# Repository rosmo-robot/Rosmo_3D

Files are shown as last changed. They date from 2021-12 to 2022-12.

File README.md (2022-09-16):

# Rosmo_3D

:warning: In development. 

It is part of the [rosmo.io](https://rosmo.io) project. You can find complete BOM on the Rosmo website.

What is Rosmo?

It's a modular set of open-hardware components that can be assembled into robots of different complexity and price.

It's all based on ESP32 so should support MicroROS work.

There are a number of different needs for 'starter' robot kits.

Software that's interesting to us right now includes:

Linorobot2 C++/ Platformio / Ros2

https://github.com/platisd/smartcar_shield/ C++/ Platformio/ Nice API

Hadabot (Micropython ROS2, Docker)

https://maker.makecode.com/#editor

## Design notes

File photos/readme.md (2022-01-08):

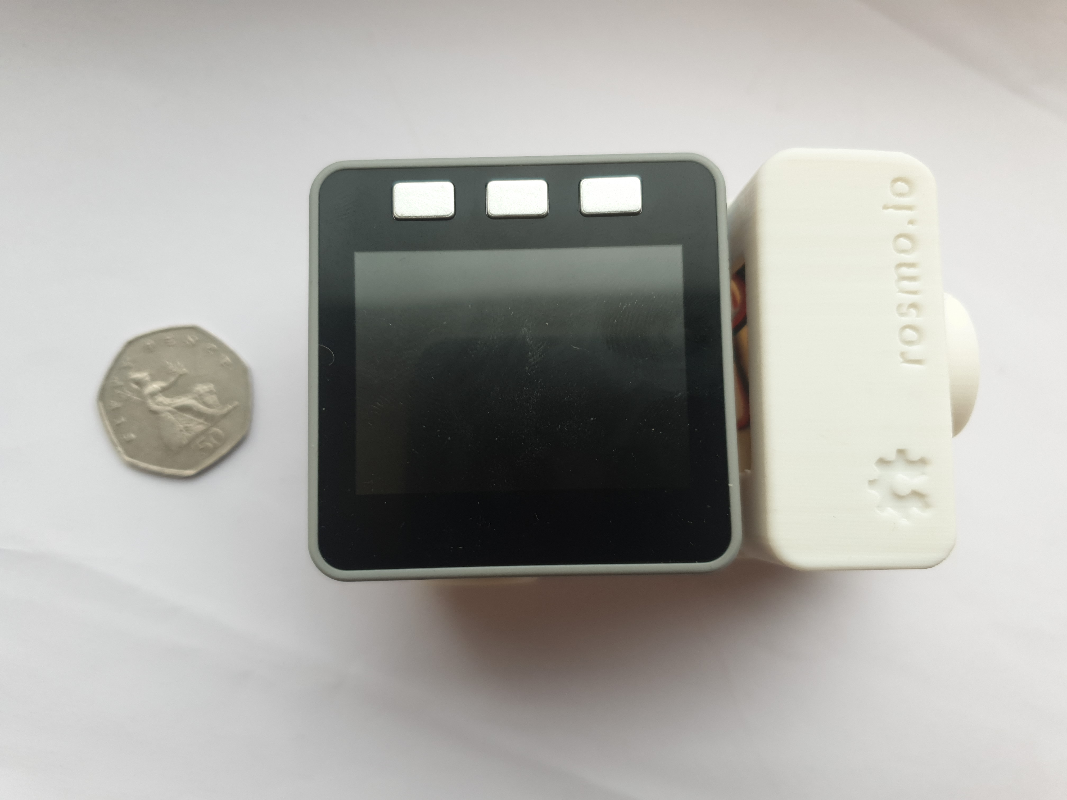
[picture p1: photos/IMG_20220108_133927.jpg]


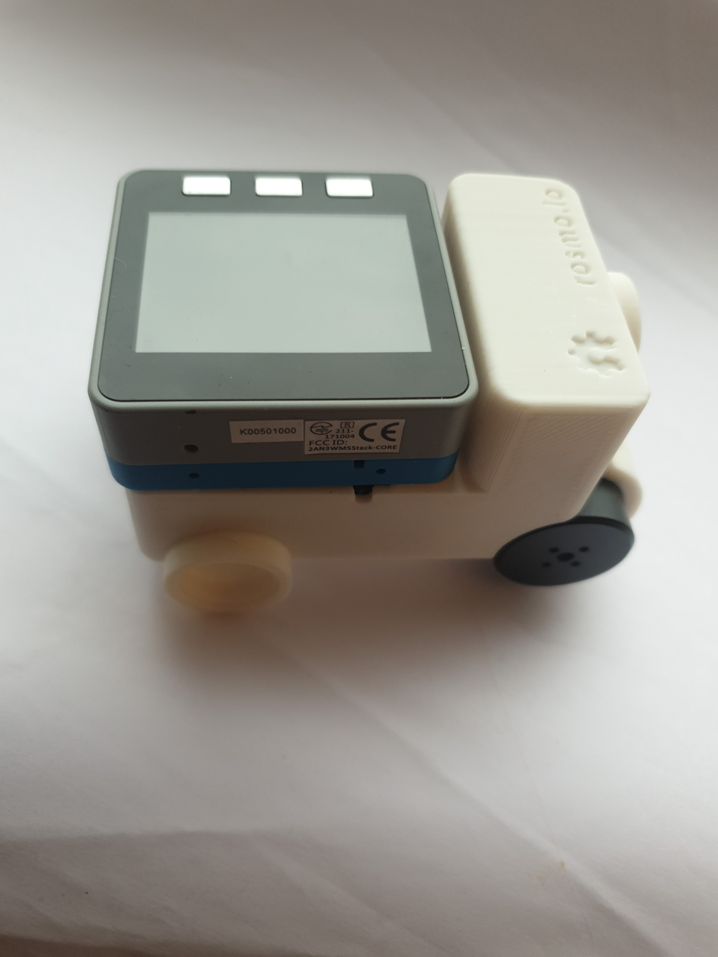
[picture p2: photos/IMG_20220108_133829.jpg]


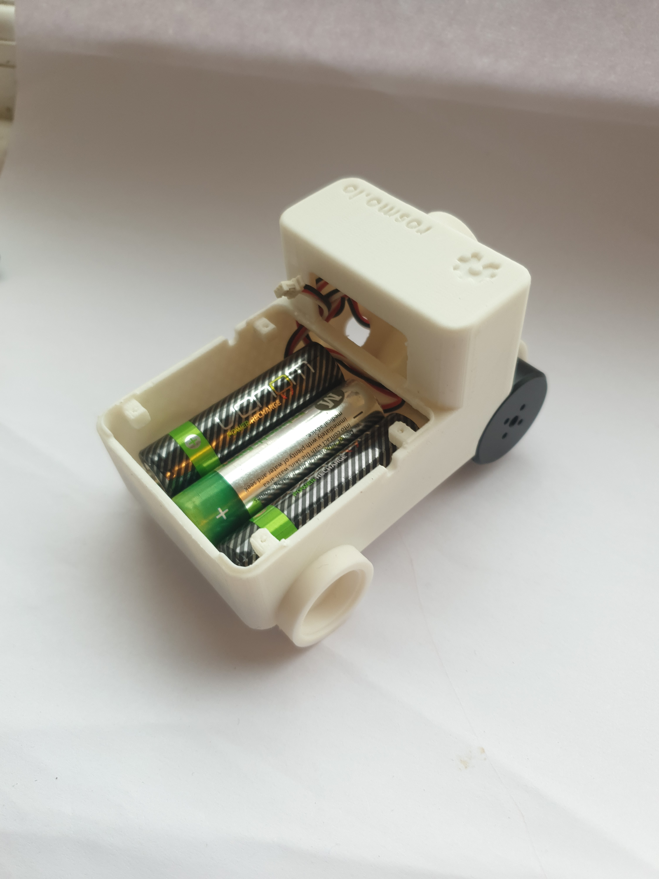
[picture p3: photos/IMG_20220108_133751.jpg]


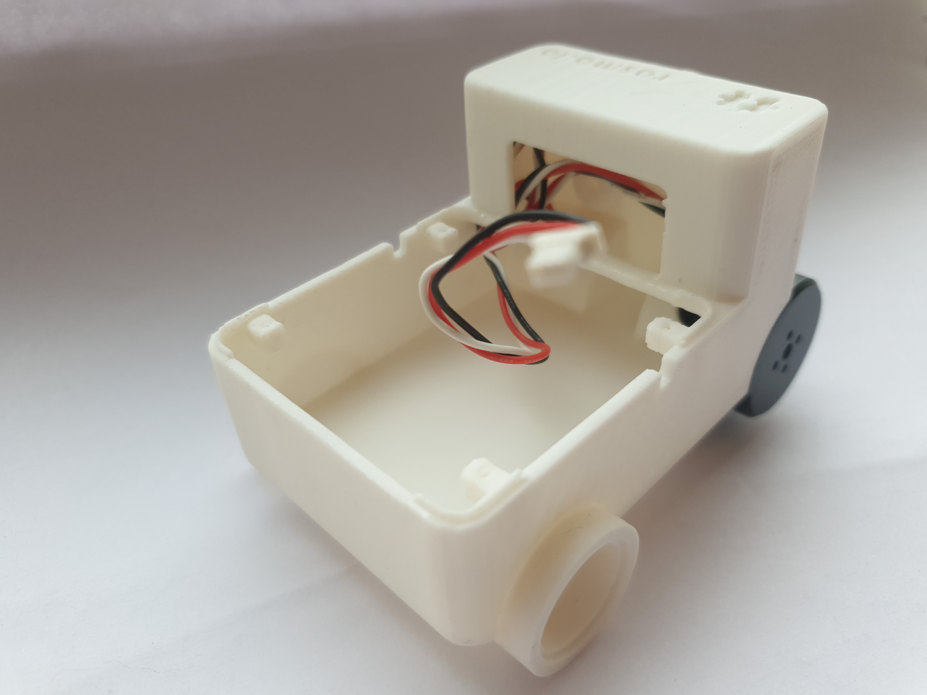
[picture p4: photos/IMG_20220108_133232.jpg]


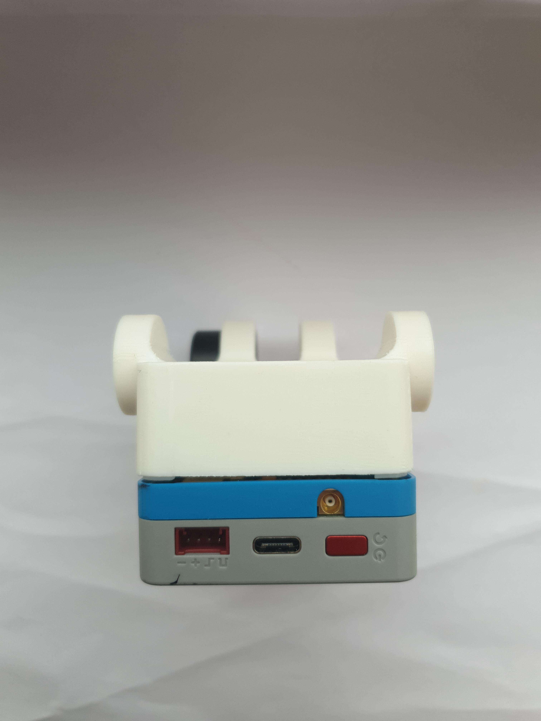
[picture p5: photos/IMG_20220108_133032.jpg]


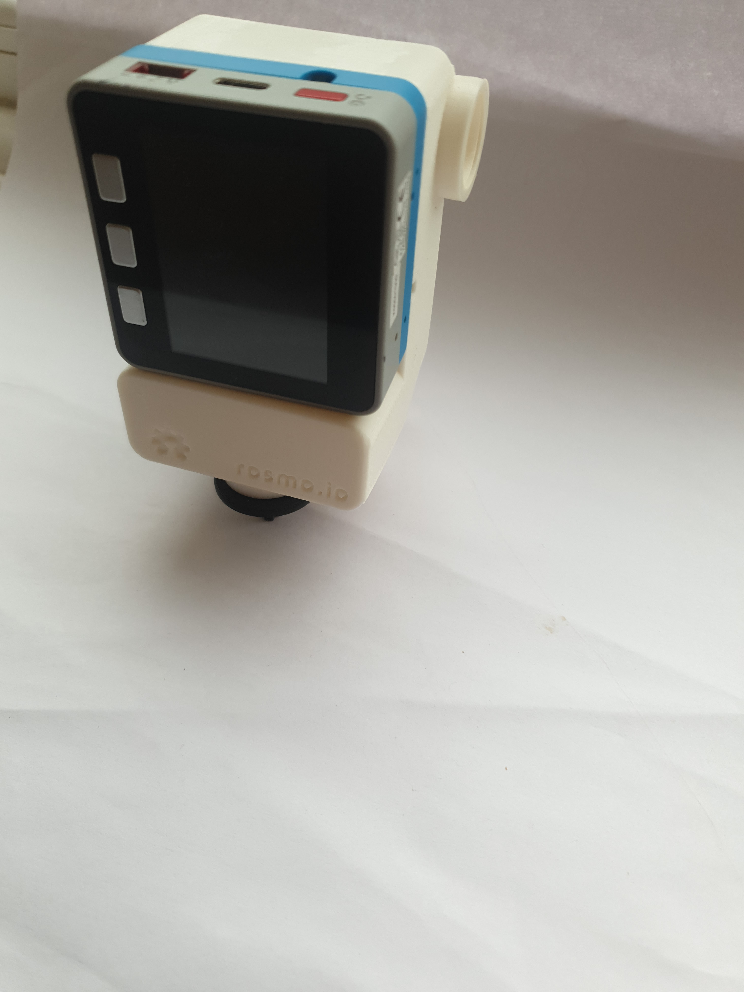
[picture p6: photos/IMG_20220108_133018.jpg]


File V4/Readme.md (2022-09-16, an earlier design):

## Brushed motor/encoder version

https://github.com/rosmo-robot/micro-bot/tree/master/Hardware/V2.11

### BLDC/encoder version additional parts

https://github.com/rosmo-robot/Rosmo_3D/blob/main/V4/BLDC/Readme.md

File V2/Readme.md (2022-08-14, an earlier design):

Design work is underway in this thread:[FreeCAD forum](https://forum.freecad.org/viewtopic.php?p=594216&sid=2a7ae776db8a154a61fe9510c4f52c36#p594216)

Check folder above with highest version number

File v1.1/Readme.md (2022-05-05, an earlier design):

This is a functional platform for motor testing

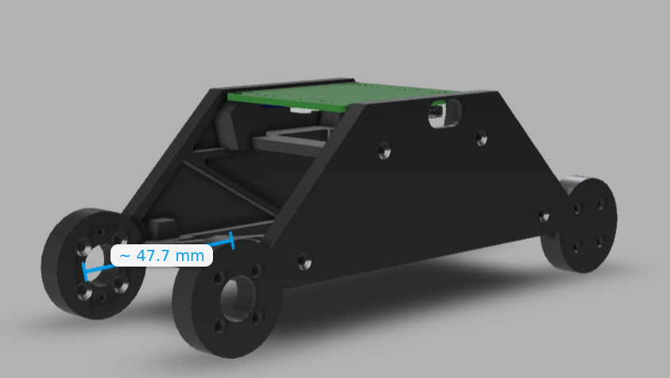
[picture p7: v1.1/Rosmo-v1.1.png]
This is an image


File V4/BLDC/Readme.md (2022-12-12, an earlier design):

### BLDC BOM

Battery

* 2x [pololu wheels](https://github.com/rosmo-robot/Rosmo_3D/blob/main/V4/pololu-rear-12mm_v4.FCStd) ([FCSTD](https://github.com/rosmo-robot/Rosmo_3D/blob/main/V4/pololu-rear-12mm_v4.FCStd))
* 1x [CamcnewPareddownH.stl](https://github.com/rosmo-robot/Rosmo_3D/blob/main/V4/servo/camcnewParedDownH-Body001Pocket036.stl)  [(FCSTD)](https://github.com/rosmo-robot/Rosmo_3D/blob/main/V4/camcnewParedDownH.FCStd) 
* 2x [encoder.stl](https://github.com/rosmo-robot/Rosmo_3D/blob/main/V2/2.09/2.09-encoder.stl) ([FCSTD](https://github.com/rosmo-robot/Rosmo_3D/blob/main/V2/2.10/Encoder-mount-v2.10.FCStd))
* 1x [RPI.stl](https://github.com/rosmo-robot/Rosmo_3D/blob/main/V4/servo/RPI.stl) mount plate ([FCSTD](https://github.com/rosmo-robot/Rosmo_3D/blob/main/V4/BLDC/RosmoBattPlate.FCStd))
* 1x [BLDC driver board](https://github.com/Twisted-Fields/rp2040-motor-controller) Get xt60 plug on the power, 4mm female banana on the motor cables.
* 1x [1300mah 4s battery](https://www.aliexpress.com/item/33003200541.html) 
* 2x [Magnet_Holder.stl](https://github.com/rosmo-robot/Rosmo_3D/blob/a09dbaf5618fc7efe2f3068fb2b35d144179f3ac/V2/2.10/Magnet_Holder.stl)
* 2x [GB 2208 motors](https://www.aliexpress.com/wholesale?catId=0&initiative_id=SB_20220818074047&SearchText=gb2208)
* 1x [Huzzah 32 feather](https://www.adafruit.com/product/3405)
* 1x [Feather:bit](https://github.com/rosmo-robot/Feather-Bit/)
* 1x [16340 powerbank](https://www.aliexpress.com/item/32951637621.html)
* 1x [16340 battery](https://www.aliexpress.com/item/1005004385519421.html)

Plus you will need the [Pololu 22T kit](https://shop.pimoroni.com/products/pololu-track-set-1?variant=933150982154), or alternately print [2x front wheels](https://www.thingiverse.com/thing:885742) & [track](https://www.thingiverse.com/thing:1936113)

Or if you don't want Pololu tracks, check out the [Tamiya track parts](https://github.com/rosmo-robot/Rosmo_3D/tree/main/V2/optional-tracks)

## Optional extras

 * [2.4" screen](https://www.aliexpress.com/item/1005003936535877.html)

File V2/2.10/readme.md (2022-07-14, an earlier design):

This model was made by [Bance on FreeCAD](https://forum.freecadweb.org/viewtopic.php?p=596344#p596344). It is released under a [CERN-OHL-P licence](https://github.com/rosmo-robot/Rosmo_3D/blob/main/LICENSE)

*untested 

You will need to print

* 1x v2.10-Body.stl
* 1x 2.10-battery-clip.stl
* 2x Magnet_Holder.stl
* 2x pololu-rear.stl
* 2x Encoder-mount-v2.stl

Plus you will need the [Pololu 22T kit](https://shop.pimoroni.com/products/pololu-track-set-1?variant=933150982154), or alternately print [2x front wheels](https://www.thingiverse.com/thing:885742) & [track](https://www.thingiverse.com/thing:1936113)

Or if you don't want Pololu tracks, check out the [Tamiya track parts](https://github.com/rosmo-robot/Rosmo_3D/tree/main/V2/optional-tracks)

# Changelog

1. Expanded encoder sockets
2. Motor cable can now go out up from encoder mount
3. Main tray trimmed/extended as required.
4. Changed bolt holes to through all.

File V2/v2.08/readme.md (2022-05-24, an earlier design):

The axel nut housings were too small, resized.

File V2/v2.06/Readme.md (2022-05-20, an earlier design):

This model was made by [Bance on FreeCAD](https://forum.freecadweb.org/viewtopic.php?p=596344#p596344). It is released under a [CERN-OHL-P licence](https://github.com/rosmo-robot/Rosmo_3D/blob/main/LICENSE)

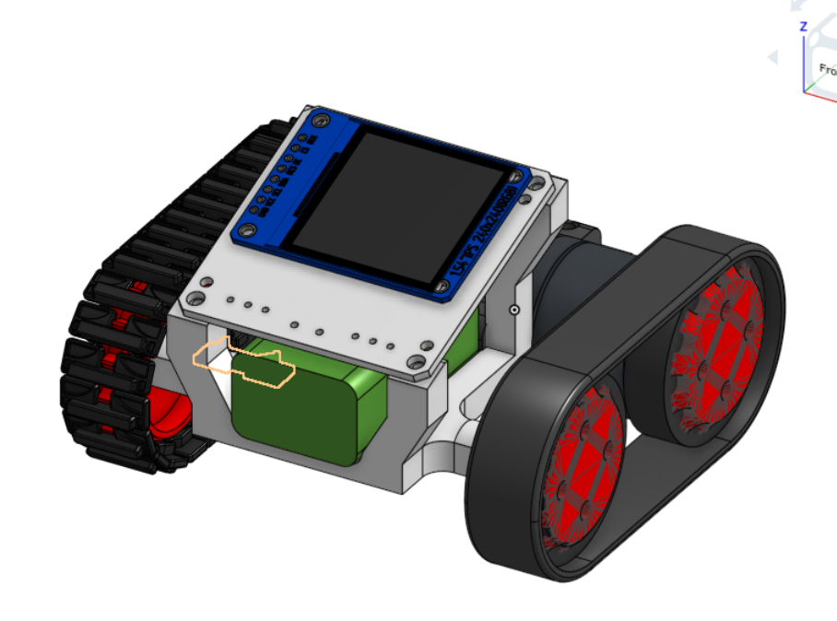
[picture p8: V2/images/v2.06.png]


[View model](https://cad.onshape.com/documents/1616bde745e05690bd2f50e3/w/f603a4efa7320437acad7441/e/d3c72be522508f10a3753235)

*untested 

You will need to print

* 1x v206.stl
* 2x Magnet_Holder.stl
* 2x pololu-rear-3.4mm.stl
* 2x v206-encoder.stl

Plus you will need the [Pololu 22T kit](https://shop.pimoroni.com/products/pololu-track-set-1?variant=933150982154), or alternately print [2x front wheels](https://www.thingiverse.com/thing:885742) & [track](https://www.thingiverse.com/thing:1936113)

Or if you don't want Pololu tracks, check out the [Tamiya track parts](https://github.com/rosmo-robot/Rosmo_3D/tree/main/V2/optional-tracks)

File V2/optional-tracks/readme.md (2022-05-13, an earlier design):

In addition to the Pololu tracks we would like to support Tamiya tracks

The Sprocket for these is https://github.com/rosmo-robot/Rosmo_3D/blob/main/V2/Sprocket.stl

It needs to be adapted as a front wheel with the [same  4mm  hole as the pololu](https://www.pololu.com/file/0J1359/pololu-track-set-dimensions.pdf)

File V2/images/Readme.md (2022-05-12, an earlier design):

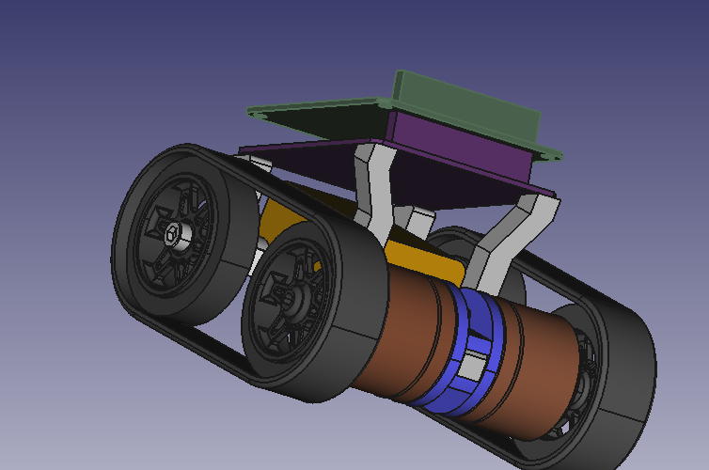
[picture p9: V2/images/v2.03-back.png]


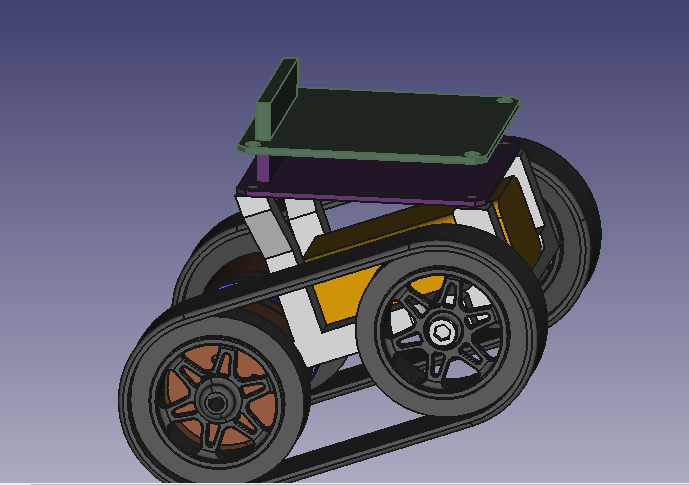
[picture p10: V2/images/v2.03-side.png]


T
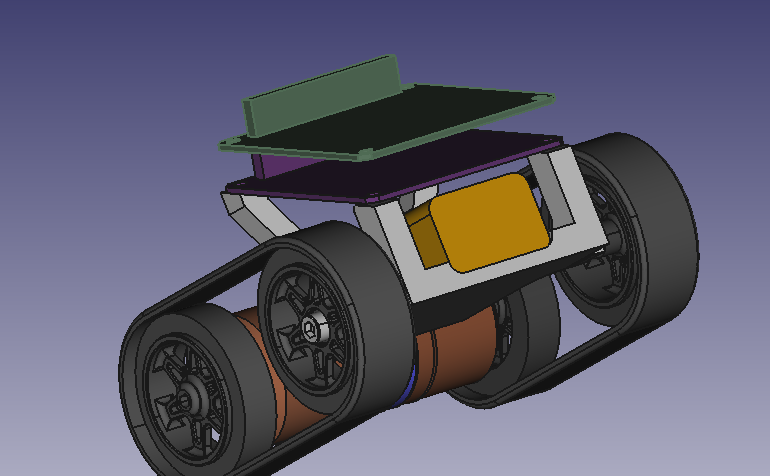
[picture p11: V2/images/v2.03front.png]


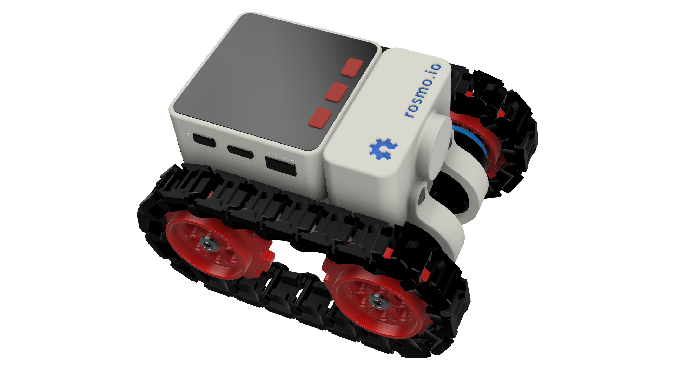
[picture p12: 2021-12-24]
rosmo.png

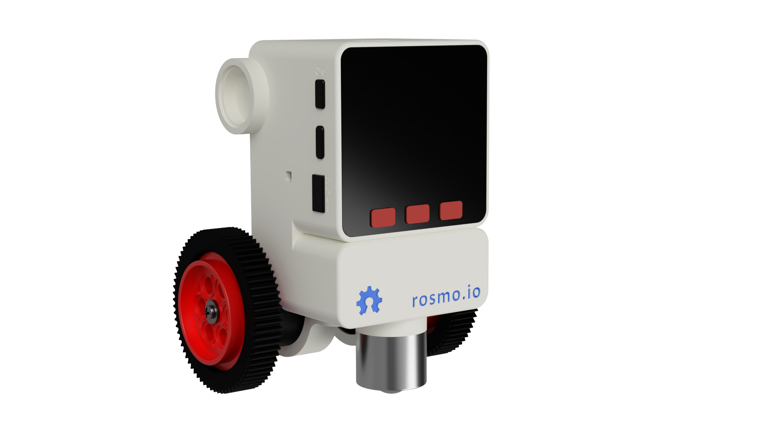
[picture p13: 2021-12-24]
wheel_mode.png

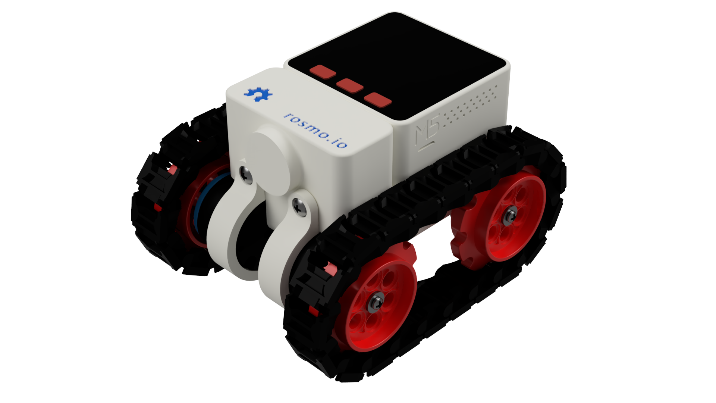
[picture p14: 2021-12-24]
track_mode.png

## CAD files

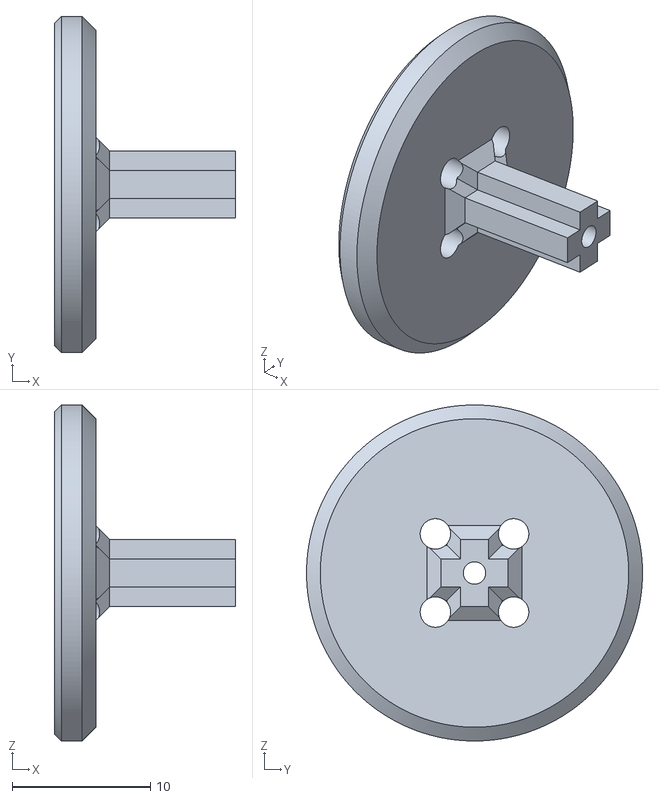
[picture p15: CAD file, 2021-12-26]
v1_wheeled/3D_Print/Connector.stl
13.1 x 24.3 x 24.3

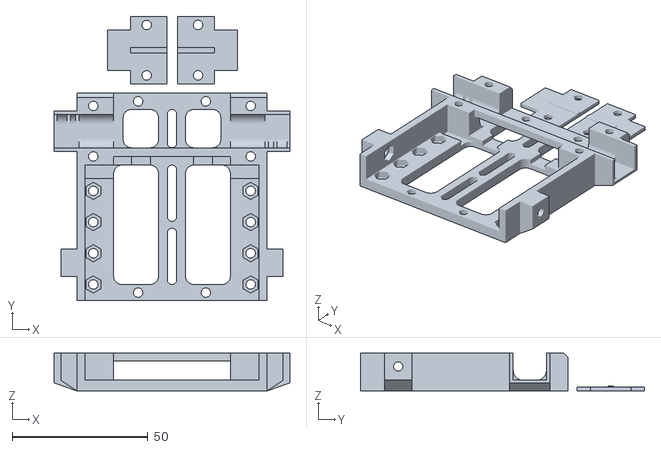
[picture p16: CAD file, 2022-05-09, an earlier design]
V2/Main_-_Chassis_and_Motor_Caps.stl
87.0 x 104.9 x 14.0

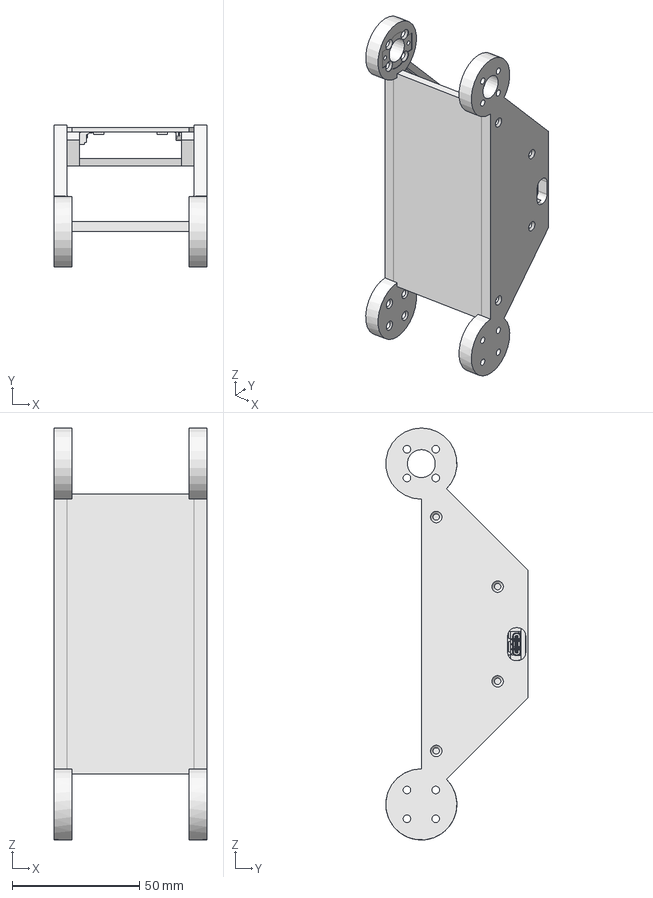
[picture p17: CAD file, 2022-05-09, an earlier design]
v1.1/rosmov1.1.FCStd
60.0 x 56.0 x 162.0 mm

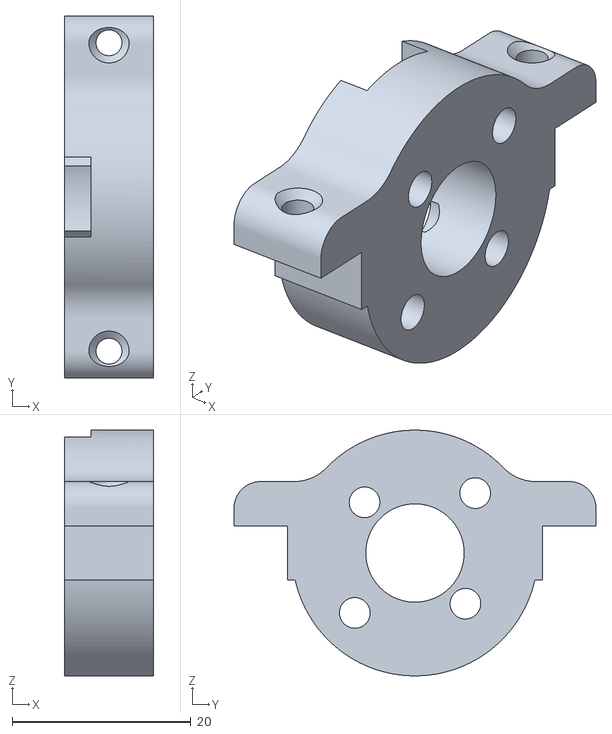
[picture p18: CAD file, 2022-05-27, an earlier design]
V2/2.09/2.09-encoder.stl
10.0 x 40.5 x 27.5

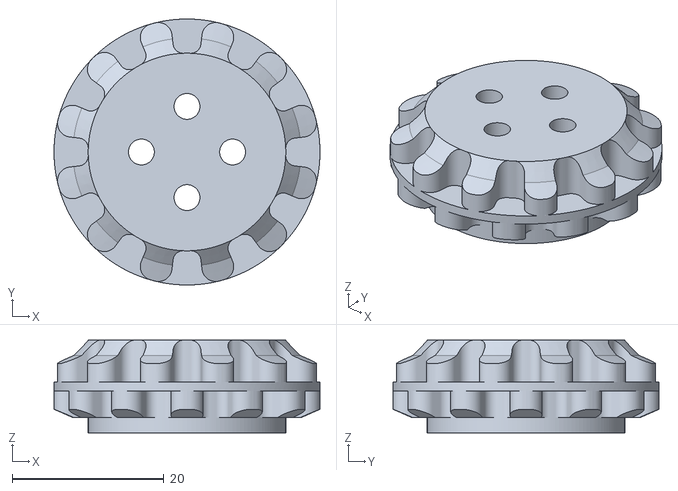
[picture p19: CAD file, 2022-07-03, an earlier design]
V2/2.10/pololu-rear-12mm_v4-Pololu_wheel_with_motor_shaft.stl
35.0 x 35.0 x 12.2

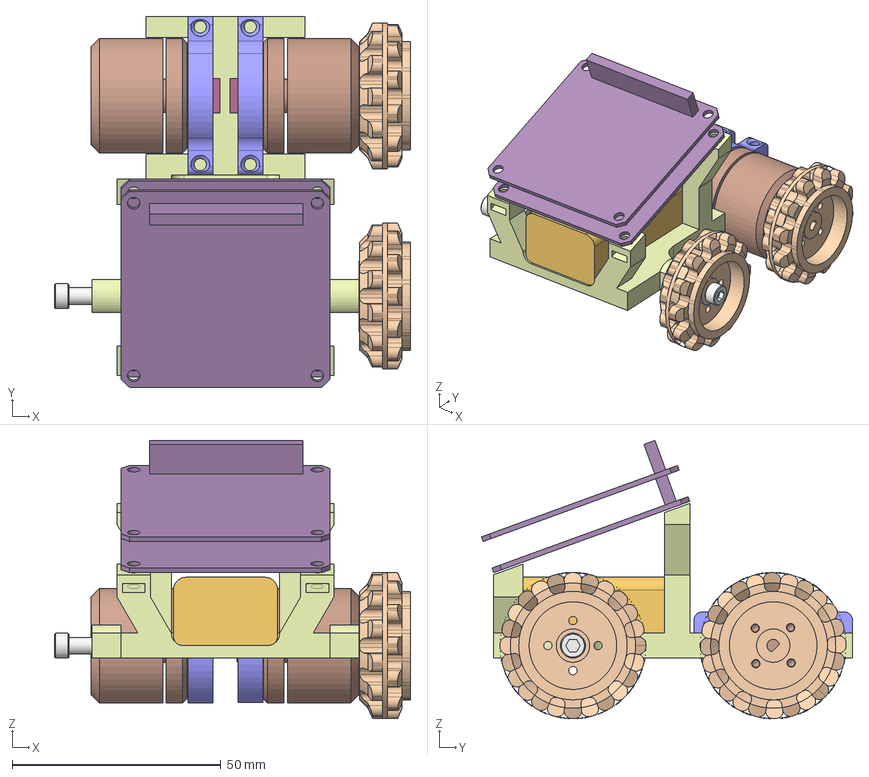
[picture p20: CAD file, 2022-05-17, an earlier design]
V2/dev/v2.05.FCStd
85.4 x 88.9 x 66.7 mm
Short thread Screw x 2
Pololu_wheel_with_motor_shaft x 2

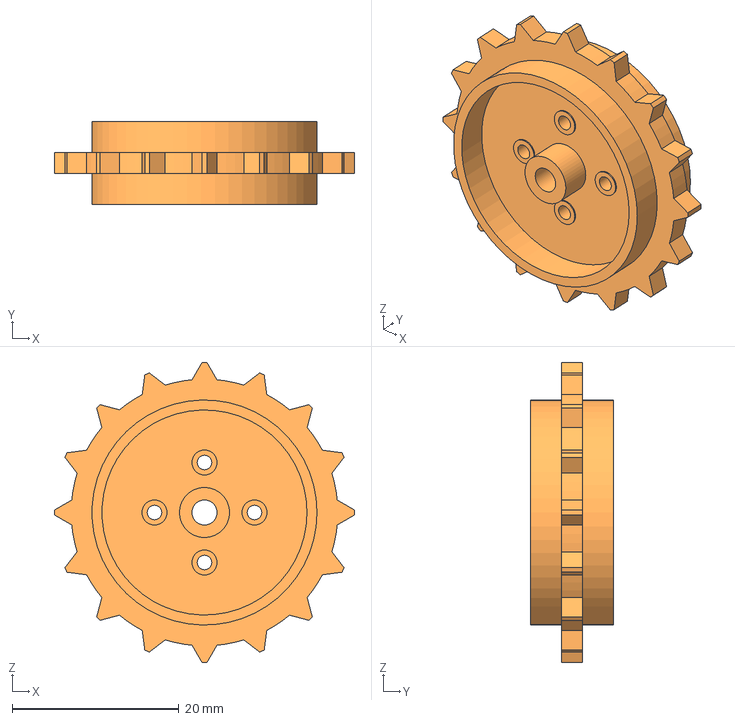
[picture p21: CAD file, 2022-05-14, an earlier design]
V2/optional-tracks/rear_sprocket_tamiya.step
36.0 x 10.0 x 36.0 mm

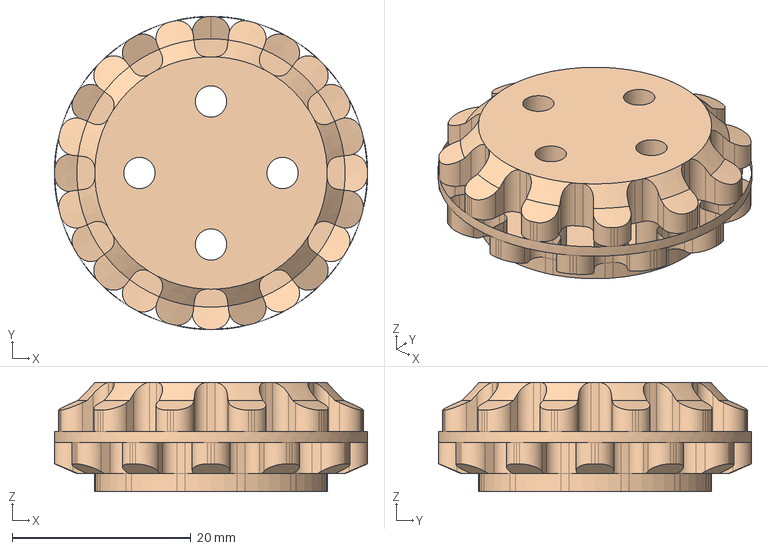
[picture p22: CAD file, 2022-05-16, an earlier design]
V2/Pololu-rear-v1.FCStd
35.0 x 35.0 x 12.2 mm

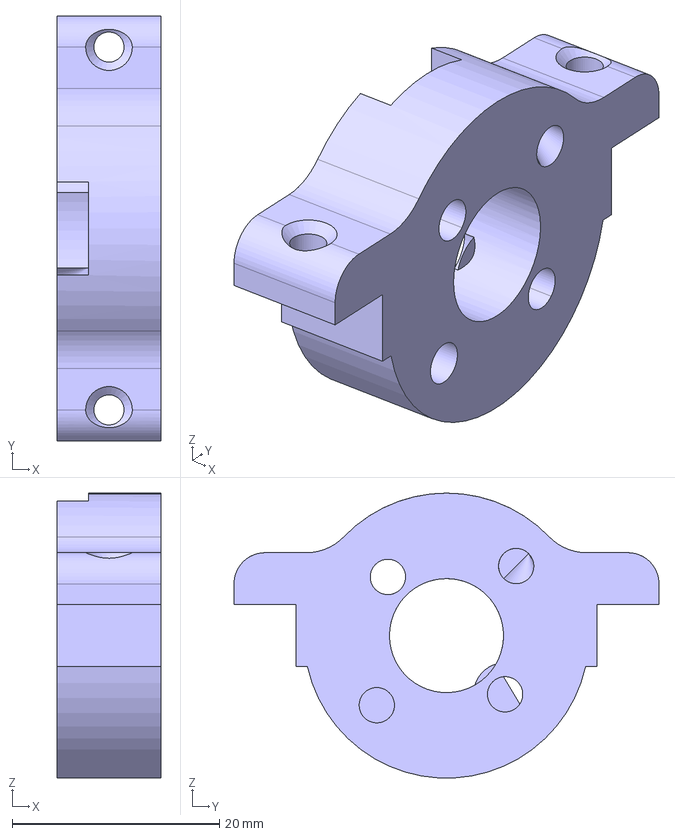
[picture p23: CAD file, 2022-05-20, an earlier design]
V2/v2.06/v206-encoder.step
10.0 x 41.0 x 27.5 mm

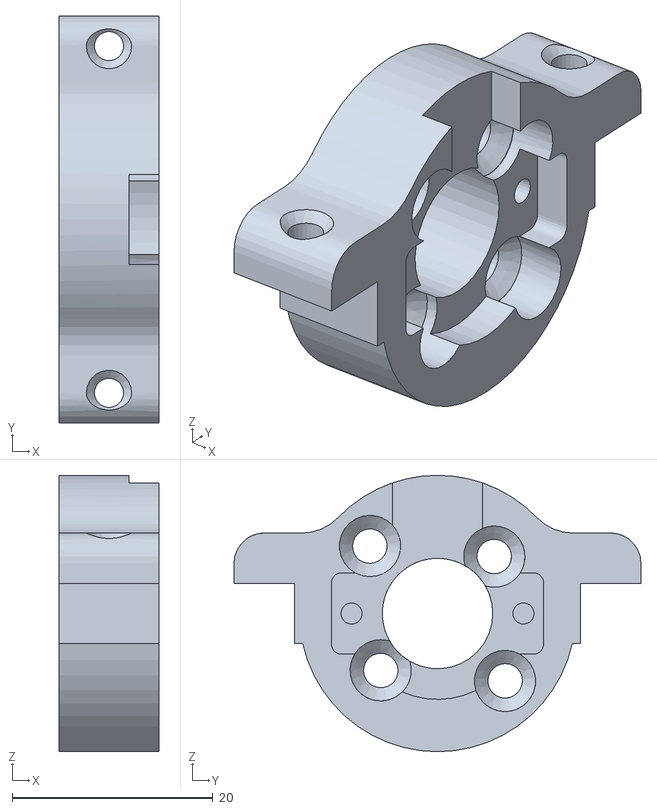
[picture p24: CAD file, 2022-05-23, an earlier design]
V2/v2.07/v.2.07-encoder.stl
10.0 x 40.5 x 27.5

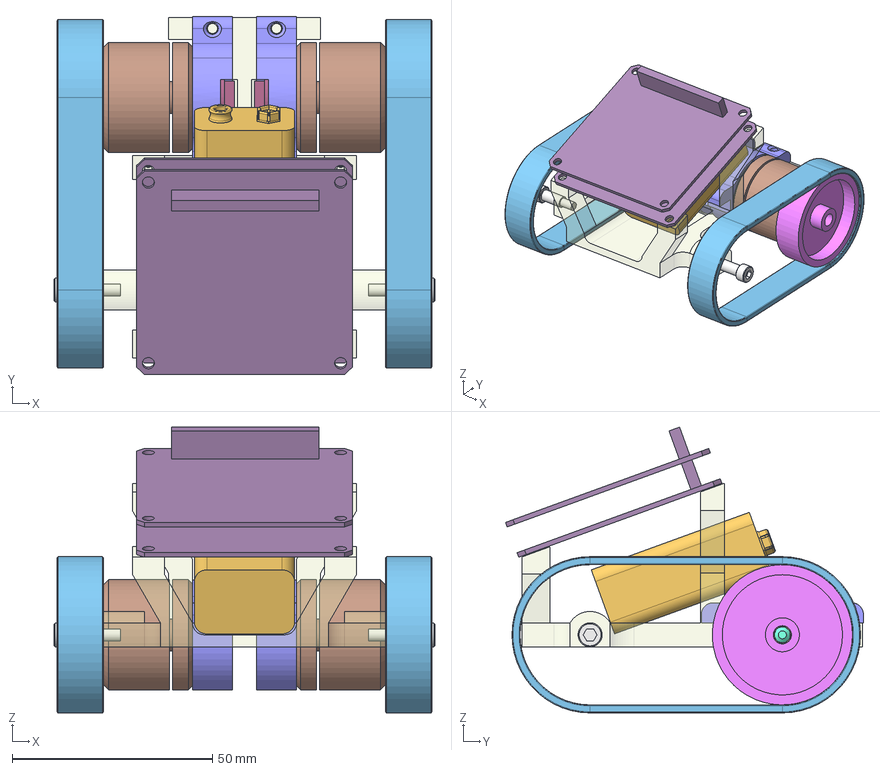
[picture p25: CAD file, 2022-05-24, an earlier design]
V2/v2.08/v2.08.FCStd
95.0 x 89.4 x 71.4 mm
Short thread Screw x 2

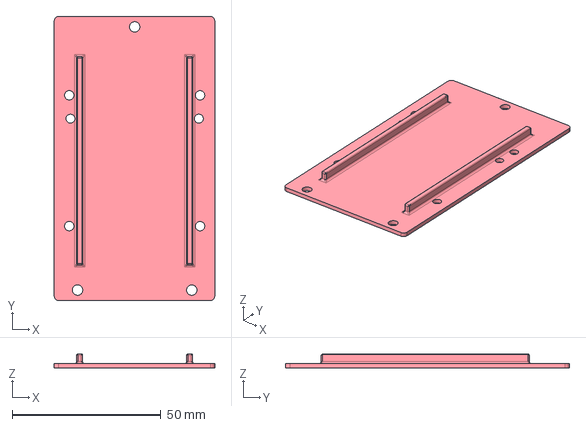
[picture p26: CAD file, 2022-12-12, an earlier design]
V4/BLDC/RosmoBattPlate.FCStd
54.0 x 95.5 x 4.75 mm

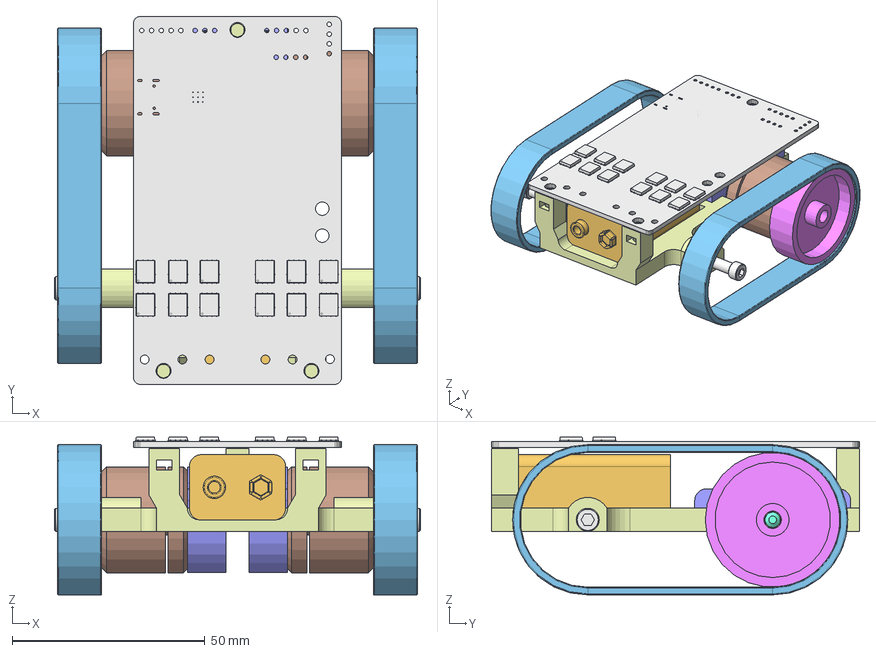
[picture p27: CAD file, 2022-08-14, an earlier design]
V4/camcnewParedDownH.FCStd
95.0 x 95.6 x 41.0 mm
Short thread Screw x 2
RPI001001

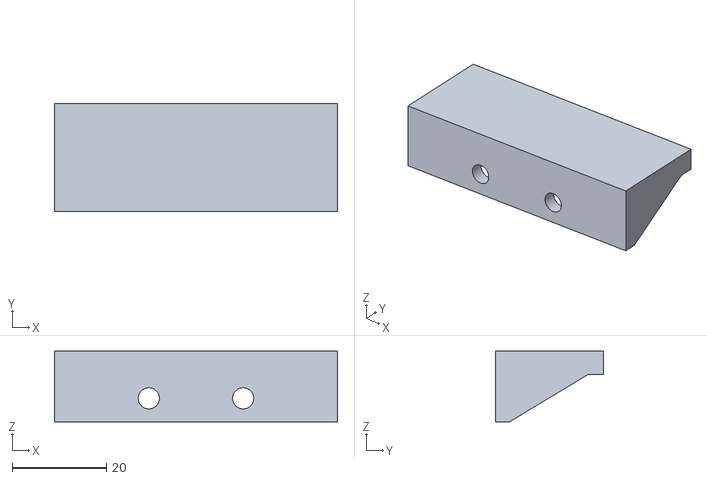
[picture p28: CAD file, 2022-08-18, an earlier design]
V4/servo/RVR_microbit_mount.STL
60.0 x 23.0 x 15.0

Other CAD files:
v1.1/Rosmo_v1_1.stp
V2/2.09/2.09.FCStd
V2/2.10/v2.10-Body.stl
V2/ChassisAnd MotorCaps.FCStd
V2/2.09/2.09.stl
V2/2.10/2.10-battery-clip.stl
V2/2.10/Encoder-mount-v2.10.FCStd
V2/2.10/Encoder-mount-v2.stl
V2/2.10/Magnet_Holder.stl
V2/2.10/v2.10.FCStd
V2/Pi_-_Camera_Mount_Plate.stl
V2/Pololu-rear-v1.stl
V2/Pololu_wheel_with_motor_shaft_easy.FCStd
V2/Pololu_wheel_with_motor_shaft_easy.stl
V2/Pololu_wheel_without_motor_shaft.SLDPRT
V2/Sprocket.stl
V2/dev/Chassis-motor.FCStd
V2/dev/Chassis-motor.stl
V2/dev/front-pololuv1.step
V2/dev/rear-pololuv1.step
V2/dev/v2.02.FCStd
V2/dev/v2.04.FCStd
V2/optional-tracks/Front_sprocket_tamiya.step
V2/optional-tracks/Sprocket_4mm_hole.stl
V2/optional-tracks/pololu-wheel.step
V2/pololu_track_22T.stl
V2/v2.06/v2.06.FCStd
V2/v2.06/v206-encoder.stl
V2/v2.06/v206.step
V2/v2.06/v206.stl
V2/v2.07/v.2.07.FCStd
V2/v2.07/v.2.07.stl
V2/v2.08/v2.08.stl
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

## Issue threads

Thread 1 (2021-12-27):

Body needs holes for ports

runger1101001, 2021-12-27:
I think I understand how the ESC PCB would attach to the body... so it would be screwed on directly to the body, and not have its own "shell". In this case, the ports need to be modelled into the body:

- USB
- Grove port
- 2xSPI (JST SH 6 pin)
- 2 pin PWR terminal
- 2x 3 pin motor phases

samuk, 2021-12-27:
Hmm I was imagining we would do it a 'shell' of it's own. I guess we'd need one for other use cases beyond the simple diffdrive in any case?

runger1101001, 2021-12-28:
Ok, in this case the design needs some updating.

The way m5 stack works, what I consider the "top" of the PCB is actually the bottom. So if you look at the ODrive module for example, the white side of the PCB (the flat side with the low connector) faces upwards and attaches to the Core module.
The black side of the PCB, with most of the components and all the headers/plugs on it, faces down. So the plugs are actually "upside down" when looking at the core module's screen.

For our design this means the top of the ESC is the side with the MCU, which will face the m5 core. The driver ICs and plugs are on the bottom side.

When you attach this PCB to the 3D designed base, the plugs would stick down into the base. If you turned it around, the m5 core would be inside the base, that wouldn't work.

samuk, 2021-12-28:
Yes makes sense. Let's see if we can attach a shell to the body. We might be able to add some press fit 'tabs' that protrude up from the body and click into corresponding holes on our ESC case? Or maybe the holes are in the tabs and the ESC case has some pin/ lumps that it mates up too?

samuk, 2021-12-30:
Will re-open as a 'tab' issue

Closed 2021-12-30.

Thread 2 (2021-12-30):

Create case for Rosmo ESC

samuk, 2021-12-30:
Create a M5 stack case for https://github.com/rosmo-robot/Rosmo_ESC

This case may be a useful start: https://www.thingiverse.com/thing:2754642

The case should include a mechanism for secure attachment to the main body of the robot. The ESC case should be stackable with other ESC cases, or other M5 modules.

Tabs/clips may need to be added to the main robot body. Or additional sockets added to accept clips. https://www.sculpteo.com/blog/2018/04/25/how-to-connect-two-parts-with-3d-printed-joints-and-snap-fits/

samuk, 2022-01-03:
@sathya131295 Here's the .step file: https://github.com/rosmo-robot/Rosmo_ESC/issues/8#issuecomment-1004401861

runger1101001, 2022-01-08:
Hey @sathya131295 , you're working in fusion 360? I have a license... is it possible that you share the fusion design so I could open it too? We've been doing it via files but it would be much cooler to have the updates via the cloud, so to speak... read-only would be fine...

sathya131295, 2022-01-09:
https://a360.co/3Gckw9p ,here is the link.

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

samuk, 2022-05-04:
Please see https://github.com/rosmo-robot/Rosmo_3D/new/main/V2

Closed 2022-05-04.

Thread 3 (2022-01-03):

Create encoder housing for BGM2208 motors

samuk, 2022-01-03:
In addition to the 2205 motors, we would like to support [2208 motors,](http://www.dys.hk/product/BGM2208-70.html)

These  BGM2208 motors do not include an enclosure for the encoder. So we need to create a 3d print part that can screw to the motor and hold the encoder firmly.

These are the encoders: https://github.com/rosmo-robot/Rosmo_ESC/issues/10#issuecomment-1004394146

samuk, 2022-05-04:
Resolved by alternate approach

Closed 2022-05-04.

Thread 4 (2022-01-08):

Create case for Open Core

samuk, 2022-01-08:
A 3d printed case to hold the open core board.

samuk, 2022-05-04:
Please see https://github.com/rosmo-robot/Rosmo_3D/new/main/V2

Closed 2022-05-04.

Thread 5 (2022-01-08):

Create 'open wheel' for certification

samuk, 2022-01-08:
For certifying the robot as OSHW we can't use any proprietary components such as lego. Therefore we should create a simple wheel of the same diameter as the lego one, which can be screwed directly to the motor.

sathya131295, 2022-01-19:
Sure

sathya131295, 2022-01-19:
Open wheels: https://a360.co/3AesEEg

samuk, 2022-01-19:
Looks great, Thanks!

Closed 2022-01-19.

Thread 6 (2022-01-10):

Give Rosmo a face/ cover

samuk, 2022-01-10:
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

To complement the open core case: https://github.com/rosmo-robot/Rosmo_3D/issues/4 which simply holds the board in the M5 stack.

 This is a 'cover' that could be attached to the basic case. The cover should have partially cutout holes to take an optional [HCSR04](https://www.aliexpress.com/af/hc-sr04.html)

I like what they've done here: https://www.aliexpress.com/item/4000232196600.html could we steal that? Have some cutouts like that to make a 'face'.

samuk, 2022-01-19:
@sathya131295 Do you fancy having a go at this one sometime? It would only be functional when in the wheel mode.

samuk, 2022-05-04:
Please see https://github.com/rosmo-robot/Rosmo_3D/new/main/V2

Closed 2022-05-04.

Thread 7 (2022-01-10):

Rosmo design guidelines & colour palette(s)

samuk, 2022-01-10:
**Features to include somewhere on PCB silkscreen**
[Open hardware logo](https://www.oshwa.org/open-source-hardware-logo/)
Licence: https://ohwr.org/cern_ohl_p_v2.txt
https://rosmo.io
Copyright: Primary author name - year
Version number V1.X

Anyone can make any of these bits in any colour they choose. In terms of the colours we use for bits, we produce & put on the website/social media I propose.

**'Default' colours - White/Red/Black**
White solder mask. Black silkscreen
White robot body
White cases.
Black lego wheels.
Red [Face](https://github.com/rosmo-robot/Rosmo_3D/issues/6)
(Will also look good with [official M5 in white](https://shop.m5stack.com/collections/stack-series/products/m5stack-core2-esp32-iot-development-kit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) or [red](https://shop.m5stack.com/collections/stack-series/products/m5stack-fire-iot-development-kit-psram-v2-6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))

**Pink colour**
White solder mask. Black silkscreen
Pink robot body
Pink cases.
Black lego wheels.
Pink [Face](https://github.com/rosmo-robot/Rosmo_3D/issues/6)

**Black/Yellow colours**
White solder mask. Black silkscreen
Black robot body
Black cases.
Yellow lego wheels.
Yellow [Face](https://github.com/rosmo-robot/Rosmo_3D/issues/6)
(Will also look good with official M5 in [black](https://shop.m5stack.com/collections/stack-series/products/esp32-basic-core-iot-development-kit-v2-6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) or [yellow](https://shop.m5stack.com/collections/stack-series/products/m5stack-core2-esp32-iot-development-kit-for-aws-iot-edukit))

runger1101001, 2022-01-10:
Ouch, one day late on this issue...

Hmmmm....  do you mean red solder mask, white silk screen? The PCB colour itself is not really choosable, FR4 is a kind of dull yellow/khaki colour, and copper is copper. Plating can be tin or gold (ENIG), I think I went for tin to keep the costs down.

Red solder mask would be available, but adds 2 days to fabrication time because it is less commonly ordered, I presume.

At the moment I have ordered the board in white solder mask, black silk screen, because that's what the other m5 modules generally seem to use. If you care strongly about the colour of the prototypes I can ask the service rep to change the order, but I'd prefer not to. The v2 board shall be red, now that I know. :-)

samuk, 2022-01-10:
Cool, all good :) Yes, I meant the other way around.( I shouldn't comment before coffee in the mornings..) I've edited my original comment.

Let's standardise on White PCB black silk, I don't feel strongly about it.

runger1101001, 2022-01-10:
Logo yes, the other two no... but I will add them now so the next boards have them.

samuk, 2022-01-19:
Can still link to closed issues

Closed 2022-01-19.

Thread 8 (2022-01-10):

Part "Connector" is too fine

runger1101001, 2022-01-10:
Hey, on this part:

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

the centre post is very fine. We'd be screwing an M2 screw into a very narrow, tall shape, and the distance to the edge as you see in the pic is only 0.6mm. I think my printer will produce this piece, but it will break for sure. Things will go better if one inserts the connector into the sprocket (which will then hold it together) first, before the screw, but my prediction is it will still break.

I would suggest a different approach: use the m2 screws, but go through the big holes on the sprocket. You could use 3 screws, that should be plenty. The connector can have 3 mating parts which extend into the holes and guide the screws.

And while it is possible to screw an M screw directly into printed plastic, and it will hold quite well, the caveat is that this works only once. If you unscrew it and re-screw it, the connection will no longer be good. So to enable a robot that people can assemble and disassemble multiple times I would strongly urge the use of (sunken) nuts rather than screwing into the plastic.
I use square nuts which look cool, but are also less likely to "strip" the plastic than hexagonal ones because they're less round. You just make a square pocket for the nut at the end of the screw hole.

The other thing I do is use threaded inserts which you sink into a correctly sized hole in the plastic using a soldering iron. The screws can then be nicely screwed in and out of the insert. But this is definately a bit harder, requires the soldering iron, and the inserts cost a lot more than the square nuts which cost next to nothing.

sathya131295, 2022-01-11:
Thank you for noticing. Look at the updated designs for "Connector" and "Connector2" here: https://a360.co/3Gckw9p
Let me know your view.

samuk, 2022-01-18:
Looks great, thanks

Closed 2022-01-18.

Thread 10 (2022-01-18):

Add lego profile to part of chassis

samuk, 2022-01-18:
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

If we add [Lego](https://www.thingiverse.com/thing:615256/files) bumps to this part of the chassis we could clip servos to the side of it.

samuk, 2022-01-19:
@sathya131295 are you interested in doing this? The use case would be to attach small servos to convert into a walking robot.

sathya131295, 2022-01-19:
Can do.

sathya131295, 2022-01-20:
@samuk Adding lego dots wont be an issue, but if the print orientation is not vertical, it might not fit well.

This orientation will work
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

This orientation might not work
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

samuk, 2022-01-20:
Could you expand on this?
Is it that;

If attached to the side of the robot the lego connection will have an insufficient force to hold a lego piece? Because 3dprint lego doesn't fit well?

Or is it another issue I'm not understanding?

sathya131295, 2022-01-20:
Yeah, 3D printed lego connection won't be that strong. Also, anything mounted on the side will be a cantilever.

samuk, 2022-01-20:
OK thanks. Let's scrap that idea.

Closed 2022-01-20.

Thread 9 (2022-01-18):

Reduce size of 'rear connector' to correspond to lego hole

samuk, 2022-01-18:
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

The connector part is too large and does not fit into the wheel

sathya131295, 2022-01-19:
-0.5mm reduction on all sides would do?

samuk, 2022-01-19:
Yes i think so.

samuk, 2022-01-19:
The circular part could do with being around 1mm thicker too I think to give clearance between lego sprocket and robot body
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

runger1101001, 2022-01-19:
hey, as an aside comment, for my 3D-printable designs with press-fitting parts or screw-holes, I always introduce a parameter (I call it "tolerance" but I'm sure there's a better name).
I use this parameter on all the close-fitting parts, either adding or subtracting it from the dimension involved. Then I can adapt the model to new 3D printers or filaments just by changing one parameter.

I have 3 printers and like to try different materials now and then. And I can tell you that each printer and material have slightly different properties regarding dimensional accuracy.

0.5mm is the kind of tolerance that needs to be changed depending on the printer, filament and how "tight" you want the fit to be. Depending on these things I might set it to 0.0, 0.25, or even 0.8...

Often I will then export a series of STLs with slightly changed tolerance settings, print them all, and see which fits best...

samuk, 2022-01-19:
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

This connector should match the front connector in terms of depth? So that front and rear wheels align

sathya131295, 2022-01-19:
@runger1101001 Yes, I too call it "tolerance",  a well calibrated printer can do with 0.2mm tolerance is guess.
@samuk I shall increase the size of all the slots by 0.5mm.

sathya131295, 2022-01-19:
Added some clearance for "rear connector"

Closed 2022-01-19.

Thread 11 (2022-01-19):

Reduce size of front 'connector' to fit bearing & lego

samuk, 2022-01-19:
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

This part is too large for bearing.

It is also too large for lego as discussed in other ticket.

sathya131295, 2022-01-19:
Reduced the dia by 0.5mm and added a draft angle of 1 degree.

samuk, 2022-01-19:
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

Can you double-check this part, please? Looks like we may have gone too small for a press fit in the bearing?

sathya131295, 2022-01-20:
The shaft dia is correct, i imported the wrong bearing design, will fix it now.

sathya131295, 2022-01-20:
Please verify now.

samuk, 2022-02-26:
Nice.

Closed 2022-02-26.

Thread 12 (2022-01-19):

Enlarge front bearing hole on robot body

samuk, 2022-01-19:
The bearing (as specced on https://rosmo.io) is too large to fit into the robot body.

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

sathya131295, 2022-01-19:
Updated with 17.5mm Dia

samuk, 2022-01-19:
Nice thanks :)

Closed 2022-01-19.

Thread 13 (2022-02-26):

Create alternate front wheel

samuk, 2022-02-26:
We’d like to try adapted versions of the wheel to attach directly to the bearing and motor.

The track used will be [this](https://es.aliexpress.com/item/32921129749.html)

The task is to create two versions of [this part](https://www.thingiverse.com/thing:4737213) a front version and a back version.

The front-wheel will have the features in the images below.

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

The bearing pin will screw to the robot body.

runger1101001, 2022-02-26:
Note that I already have fusion files for the above if anyone needs.
I'm also working on getting something that looks like Rosmo in a form that I can print and build it.

runger1101001, 2022-02-26:
I think it would be good to find some better tracks. I know lego is nice because available and standardised, but even many lego models use rubber tracks. This is because the linked lego tracks are much too weak in practice. They can work well in a stationary device of some kind, but as robot tracks they are too weak. Depending on the robots weight and the motor's power, even just normal acceleration can pull them apart, and on carpet the shear-forces of any kind of turn have a tendency to pull them apart.
I think we should find some suitable rubber/nylon/silicon tracks and then design the wheels for those.

samuk, 2022-02-26:
> Note that I already have fusion files for the above if anyone needs.

Ah great, I didn't realise that. Could you stick them [here](https://github.com/rosmo-robot/Rosmo_3D/tree/main/v1_optional_tracks)? I think @arj may be up for having a go at the lego one.

I take your point on rubber tracks, I'll have a look and see if I can find any.

samuk, 2022-02-28:
I wonder if there's something suitable here: https://www.robotdigg.com/category/21/Endless-Belts

runger1101001, 2022-02-28:
:-) I've ordered belts from robotdigg before... they have a lot of different ones... maybe a v-shaped one could work. But maybe something that is supposed to be a track would work even better

Printing them in TPU could work. It's not the most forgiving 3D printing material, but I have printed a bunch of tires and tracks in Ninjaflex (TPU) and they come out pretty well. There is a lot of stringing and the material is impossible to sand and very hard to cut because its so flexy. As long as there are no fine structures you can get pretty decent results. The pics on thingyverse are quite accurate for what you can expect.

Tracks could also be tensioned by a third, higher up wheel, but of course that adds more cost in the form of 2 extra bearings...

I'll search around a bit more. I found some model tank tracks on AliExpress, but they looked a bit dubious.

runger1101001, 2022-03-02:
These are pretty cool, but of course a bit expensive: https://www.gobilda.com/badlands-tank-track-24mm-pitch-112mm-width-rubber-tread-6-pack/

These use pins like a wrist-watch:
https://toykidmama.com/doit-plastic-track-for-damping-robotic-smart-car-model-chain-for-tracked-vehicle-clawler-track-type-tank-accessory-diy-rc-toy-3952skn2

A compendium of home-made tracks:
https://www.intorobotics.com/inspiration-diy-tank-treads-collection/

runger1101001, 2022-03-02:
Those pins are definitely not FDM printable...

samuk, 2022-03-02:
Sure, I was thinking something along the lines of [these pins](https://www.aliexpress.com/item/4000309875370.html), maybe M1.5 if we can find them?

samuk, 2022-05-04:
Please see https://github.com/rosmo-robot/Rosmo_3D/new/main/V2

Closed 2022-05-04.

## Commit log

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2021-12-26 Warning - Untested
    Draft of body
    [rosmo_v1_main.stl]
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2021-12-26 Part that screws to motor
    [Connector.stl]
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2022-01-19 Delete rosmo_v1_main.stl
    Newer version added
    [rosmo_v1_main.stl]
2022-01-19 Delete Connector.stl
    In wrong place now we have open wheels
2022-01-19 Delete Connector2.stl
    In wrong place
    [Connector2.stl]
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2022-01-20 Point at rosmo.io for BOM
    fix
2022-04-06 Sprocket for Tamiya tracks
    From https://drive.google.com/drive/folders/1yd4rb3Q03rMzx-B8ZvO9E6WHDlMpRS5U
    Apache licences by https://twitter.com/neet2121
    [Sprocket.stl]
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2022-05-05 Add files via upload
    Initial files
    [Rosmo_v1_1.stp]
2022-05-05 Fusion 360 source file
    [Rosmo_v1_1.f3z]
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2022-05-06 Sprocket for Pololu track/wheel byAl_batarris
    Sprocket for Pololu track/wheel byAl_batarris licensed under theCreative Commons - Attribution - Share Alikelicense. https://www.thingiverse.com/thing:885742
    [Pololu_wheel_without_motor_shaft.SLDPRT]
2022-05-06 Add files via upload
    track for mini sumo pololu style 22T byandiliis licensed under theCreative Commons - Attributionlicense. https://www.thingiverse.com/thing:1936113
    [pololu_track_22T.stl]
2022-05-08 Add files via upload
    track for mini sumo pololu style 22T byandiliis licensed under theCreative Commons - Attributionlicense. https://www.thingiverse.com/thing:1936113/files
    [Pololu_wheel_with_motor_shaft_easy.stl]
2022-05-08 First approximation of Pololu_wheel_with_motor_shaft_easy.stl
    [Pololu_wheel_with_motor_shaft_easy.FCStd]
2022-05-08 Changed license to CERN-OHL-P, cleaned original mesh data
    [Pololu_wheel_with_motor_shaft_easy.FCStd]
2022-05-09 CC-BY LiTero body
    Body from this bot: https://www.thingiverse.com/thing:2896668/files
    LiTeRo - The Little Telepresense Robot Kit byPhysics_Dudeis licensed under the Creative Commons - Attribution license.
    [Main_-_Chassis_and_Motor_Caps.stl]
2022-05-09 LiTeRo CC-BY camera mount plate
    This could maybe be repurposed into a part to hold the M5 stack boards
    LiTeRo - The Little Telepresense Robot Kit byPhysics_Dudeis licensed under theCreative Commons -https://www.thingiverse.com/thing:2896668 Attributionlicense.
    [Pi_-_Camera_Mount_Plate.stl]
2022-05-09 Add files via upload
    FreeCAD version of STEP generated by Fusion360
    [rosmov1.1.FCStd]
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2022-05-10 Original dimensions
    CERN-OHL-P. By Bance
    https://forum.freecad.org/viewtopic.php?f=8&t=68541&sid=6e242e2728a9886a33852b46f9021f17&start=10
    Derived in part from https://www.thingiverse.com/thing:2896668
    LiTeRo - The Little Telepresense Robot Kit by Physics_Dude is licensed under theCreative Commons - Attribution license.
    [ChassisAnd MotorCaps.FCStd]
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2022-05-10 WIP motors in approximate position
    [Chassis-motor.FCStd]
2022-05-14 CERN-OHP-P
    Copyright Rosmo.io https://github.com/rosmo-robot/Rosmo_3D/blob/main/LICENSE
    By Bance: https://forum.freecadweb.org/viewtopic.php?p=595099#p595099
    [v2.04.FCStd]
2022-05-14 Tamiya Sprocket - 4mm centre hole.
    Copyright (c) 2021 Rosmo
    CERN Open Hardware Licence Version 2 - Permissive
    Designed by Khalid https://twitter.com/WhenOwlsHoot
    [Sprocket_4mm_hole.stl]
2022-05-14 Front and rear pololu step from Freecad
    [front-pololuv1.step, rear-pololuv1.step]
2022-05-14 Sprockets for Tamiya 70100
    https://github.com/rosmo-robot/Rosmo_3D/blob/main/LICENSE
    Designed by Khalid: https://twitter.com/WhenOwlsHoot
    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
    [Front_sprocket_tamiya.step, rear_sprocket_tamiya.step]
2022-05-15 rear wheel with bolt holes for Gb2208
    Cern-p
    [Pololu-rear-v1.stl]
2022-05-15 rear wheel for pololu and gb2208 motor
    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
    [Pololu-rear-v1.FCStd]
2022-05-16 Add files via upload
    Cern-P
    [Pololu-rear-v1.FCStd]
2022-05-16 Add files via upload
    cern-ohp-p
    [Pololu-rear-v1.stl]
2022-05-17 Add files via upload
    CERN-OHP-P
    Copyright rosmo.io 2022
    By Bance https://forum.freecad.org/viewtopic.php?p=595634&sid=82a7fb826c8baa3e0d9f75c4916910f0#p595634
    [v2.05.FCStd]
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2022-05-20 CERN-OHW-P
    Copyright Rosmo.io
    By Bance: https://forum.freecad.org/viewtopic.php?p=596344&sid=7714ab6528e7f77b29a9e46cf1e58705#p596344
    [v2.06.FCStd]
2022-05-20 CERN-OHL-P
    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
    [v206-encoder.step, v206-encoder.stl, v206.step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]
2022-05-23 Changed PCB boards to better represent M5 Stack format
    Changed model to suit revised PCB's
    [camcnewParedDownB.FCStd]
2022-05-23 Improvements to bolt holes on mount
    [v.2.07-encoder.stl, v.2.07.FCStd, v.2.07.stl]
2022-05-24 Small change to axels
    The axel nut housings were too small, resized.
    [camcnewParedDownC.FCStd]
2022-05-24 The axel nut housings were too small, resized.
2022-05-24 The axlel nut housings were too small, resized.
    Otherwise same as v2.07
    [v2.08.FCStd, v2.08.stl]
2022-05-27 Added Battery Clip
    Have added an experimental Battery Clip.
    [camcnewParedDownE.FCStd]
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2022-06-13 Add files via upload
    Main tray trimmed/extended as required.
    Changed bolt holes to through all.
    https://github.com/rosmo-robot/Rosmo_3D/pull/20/commits/147980ee13c2099ad4717e9d2a01a998b0d9f4d5
    [v2.10.FCStd]
2022-06-13 Delete pololu-rear-3.4mm-hole.FCStd
    16mm spacing
    [pololu-rear-3.4mm-hole.FCStd]
2022-06-13 Delete pololu-rear-3.4mm.stl
    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
    [pololu-rear-3.4mm.stl]
2022-06-13 Correct 12mm spacing
    May still need holes enlarging?
    [pololu-rear-12mm.FCStd, pololu-rear.stl]
2022-07-02 Correct hole sizes
    [pololu-rear-12mm_v4.FCStd]
2022-07-02 Correct hole size
    by Andresroc
2022-07-03 Correct spacing
    By Andrés Rodríguez Campo https://www.linkedin.com/in/andr%C3%A9s-rodr%C3%ADguez-campo/
    [pololu-rear-12mm_v4-Pololu_wheel_with_motor_shaft.stl]
2022-08-14 Add files via upload
    ROSMO for 2040 driver board
    [camcnewParedDownH.FCStd]
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
